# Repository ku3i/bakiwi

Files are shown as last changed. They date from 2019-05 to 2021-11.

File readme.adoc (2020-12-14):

= Bakiwi
Doc Writer <kubisch@informatik.hu-berlin.de>
v0.1, 2020-04-02
:imagesdir: ./images/

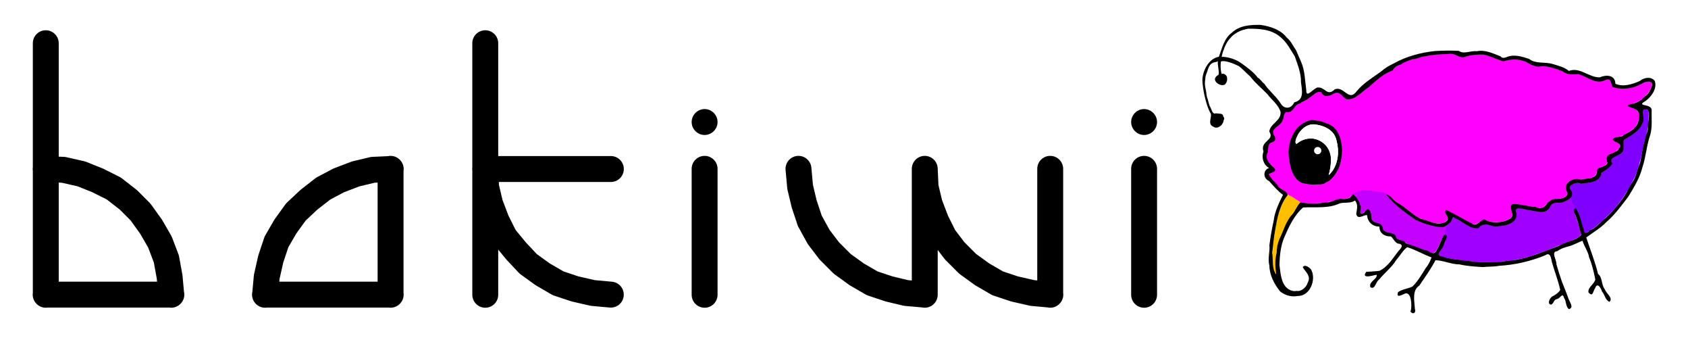
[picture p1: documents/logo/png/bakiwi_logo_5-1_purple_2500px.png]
Bakiwi


== The fabulous DIY walking robot kit.

_tl;dr: Build your own walking robot._

Welcome to the Bakiwiverse.

Bakiwis are small walking robots with only two motors that come as a kit and are easy to build. Each Bakiwi is unique. You can freely choose how it will look and behave. You can easily change your Bakiwi's walking style with four knobs mounted on the printed circuit board. Programming is not required, but have a look into the _source_ folder if you like to modify the firmware and add some nice features.

Bakiwis combine education and fun and are therefore perfect for teaching robotics to children and beginners. We have already built dozens of Bakiwis in many workshops and the builders are always amazed when their robot creature starts to walk. While it is fun to build and play with the bakiwis, many skills and technical experience are acquired.

For information on ongoing developments, you might want to follow the project on its link:https://hackaday.io/project/169268-bakiwi-robot[hackaday.io page] or follow me on link:https://twitter.com/qbernetik[twitter/@qbernetik]

== Assembly Manual

Here you can find the link:https://github.com/ku3i/Bakiwi/tree/master/manual[Bakiwi Assembly Manuals] in English and German language.

== Get a Bakiwi

We at Jetpack Cognition Lab develop, manufacture, and distribute Bakiwi Robots in our home base in Berlin/Germany. All electronic parts are RoHS compliant and the 3D-printed parts are made from PLA which is plant-based and is industrially compostable. The production of the kits takes place in Berlin-Friedrichshain and under fair conditions. If you want to *buy a Bakiwi Kit*, please visit our store: link:https://bakiwi.shop[] or consider supporting our link:https://www.kickstarter.com/projects/bakiwi/bakiwi-invent-a-robot-friend[kickstarter campaign]. 

== Videos

****
There are some video links available on how _Bakiwi_ could look when assembled and how it performs:

* link:https://www.youtube.com/watch?v=UyHHptdRnA0[Ministry of Silly Walks]
* link:https://www.youtube.com/watch?v=r7zon1IOzuM[Pulling Things]
* link:https://www.youtube.com/watch?v=ixKAcRevgqk[Bakiwicalypse]
* link:https://www.youtube.com/watch?v=EbDHLbfVccA[Human Sensing]
* link:https://www.youtube.com/watch?v=psynHG6JsZE[Workshop CCCamp19]
* link:https://www.youtube.com/watch?v=GNrDzkgFEy4[Where can I get a Bakiwi?]
****

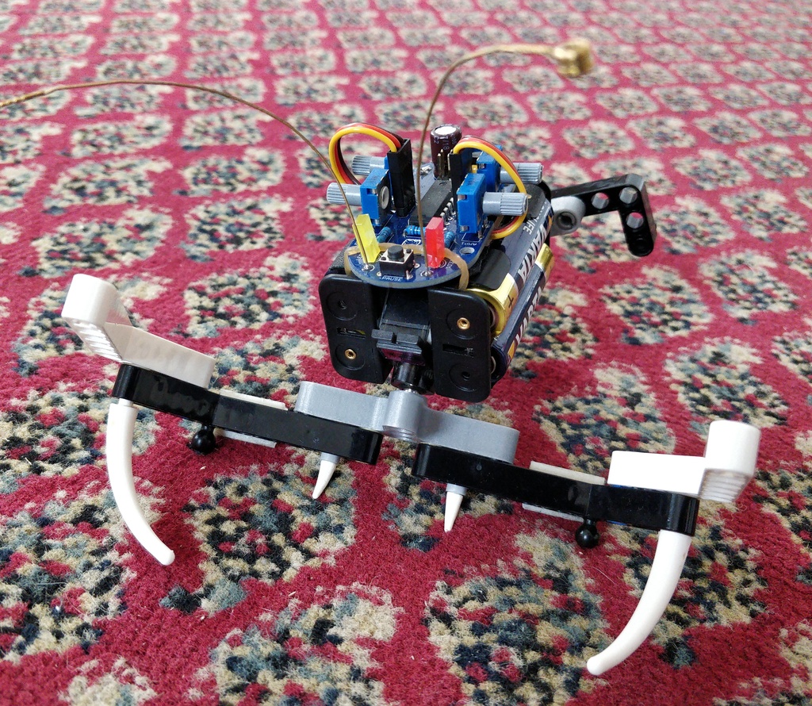
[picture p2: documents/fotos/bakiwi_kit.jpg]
Bakiwi


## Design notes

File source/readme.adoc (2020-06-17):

= Bakiwi Firmware Help
Doc Writer <kubisch@informatik.hu-berlin.de>
v0.1, 2020-04-02
:imagesdir: ./img
:toc:

_This is the Bakiwi Kit Firmware Section. Depending on your Bakiwi's hardware revision, you have to choose between different software versions._

All files of the Bakiwi firmware code is free/libre open-source software. The firmware is currently written in C/C++ incorporating the Arduino framework and some external libraries. The firmware can be deployed using the Arduino IDE.

* so2walk
* bakiwi_kit
* bakiwi_sen (*)
* plops (*)

_(*)this firmware is still under heavy development and may be subject to larger changes._

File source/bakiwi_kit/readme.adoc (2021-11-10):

= Bakiwi Install Firmware Manual
Doc Writer <kubisch@informatik.hu-berlin.de>
v0.3, 2021-11-10
:toc:

:imagesdir: ./doc

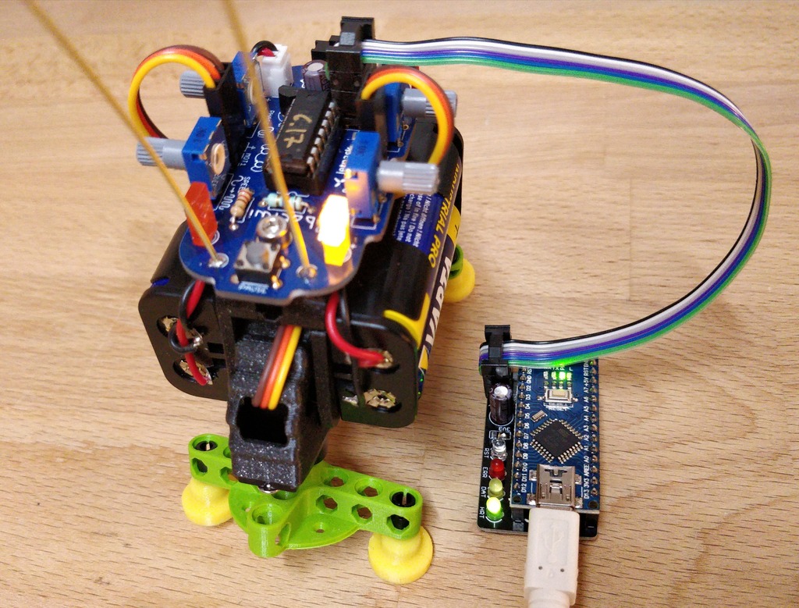
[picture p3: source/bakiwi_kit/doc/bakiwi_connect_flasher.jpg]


These instructions describe how to install or update firmware on your Bakiwi and also enable you to install a self-written program.

== Get the Programmer Device
In order to upload software to your Bakiwi you need a programmer device capable of handling AVR microcontrollers such as the Microchip ATtiny84.

There is plenty of AVR programmers available and most of them should do the job nicely. However if you are new to programming AVR microcontrollers we recommend using the ArduinoISP Kit as it works nicely together with the Arduino Integrated Development Environment (IDE).

Along with the Bakiwi Robot Kit there is the possibility to purchase a Bakiwi Programmer which comes as a solder kit.
****
`https://bakiwi.shop`
****

At the end of this document, there can be found advice on how to assemble the programmer kit.

== Get the Source Code
Clone the repository or get it via Github's download button:
****
`git clone https://github.com/ku3i/bakiwi`
****

This step requires `git`. If you're on a Linux machine, you probably have `git` already installed. You can test this by opening a terminal and typing `git --version`. If `git` is not yet installed and you want to install it, type:
****
`sudo apt-get install git`
****

== Installing the Firmware

=== Get latest Arduino IDE
Open a Browser, navigate to the following link and download the latest version of the Arduino IDE (we tested this documentation with version 1.8.12):
****
`https://www.arduino.cc/en/Main/Software`
****
=== Setup ATtiny84 Support for Arduino IDE
Start the IDE and open the `preferences` dialog. Add the following link to `Additional Boards Manager URLs`:
****
`https://raw.githubusercontent.com/damellis/attiny/ide-1.6.x-boards-manager/package_damellis_attiny_index.json`
****

Then select `Tools -> Board -> Boards Manager` and seach for `attiny`. Install the `Attiny Support Library by Davis A. Mellis`.

=== Open the Firmware Source Code and Setup Microcontroller
When the installation was succesfull open the `source/bakiwi_kit/so2walk_tiny/so2walk_tiny.ino` file via `File -> Open` dialog and setup the Attiny84 processor in `Tools` accordingly as described in the picture:

* Board: *ATtiny24/44/84*
* Processor: *ATtiny84*
* Clock: *Internal 8 MHz*
* Programmer: *Arduino as ISP* (if using a Bakiwi-ISP)

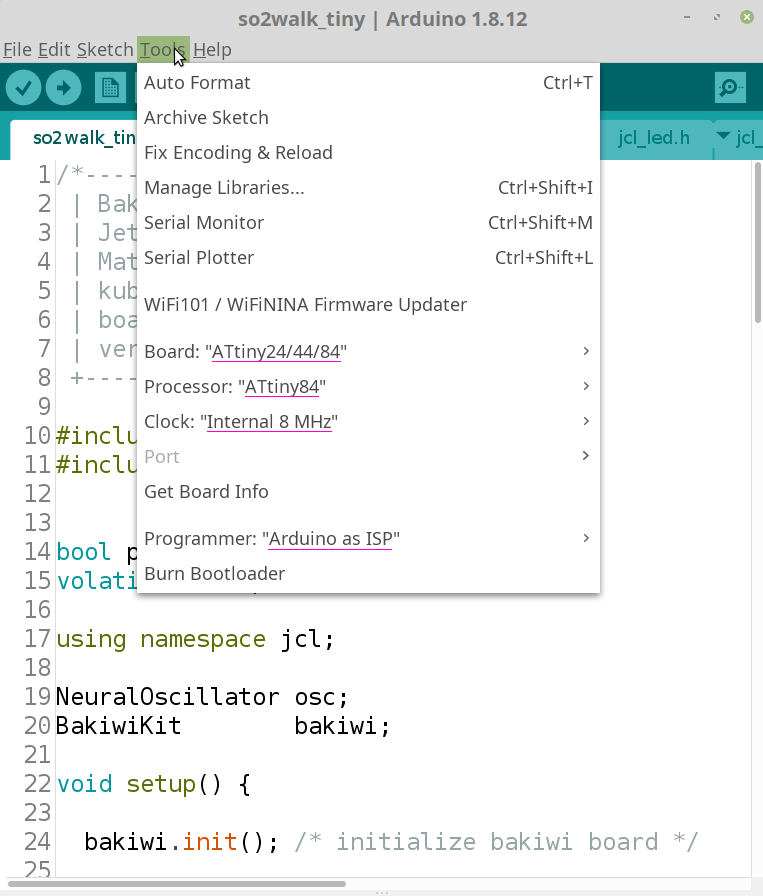
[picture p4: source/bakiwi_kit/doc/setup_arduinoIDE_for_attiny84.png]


=== Compile and Upload the Firmware

If you have set up the processor, select `Sketch -> Verify/Compile` and if the code could be successfully compiled, connect the Bakiwi-Programmer to your computer via USB cable and to your Bakiwi via the 6-pin ISP connector (pay attention to the polarity).

Then select `Sketch -> Upload` and the programmer should now start to flash the LEDs for some seconds. After that, remove the 6-pin ISP connector.

The Bakiwi-Firmware should now be installed.

== Bakiwi Programming for Experts
Your Bakiwi is always delivered with the latest firmware. However, if you want to use a brand new ATTiny84, the fuses must first be set. The following commands do exactly this and cause the LEDs to flash as a success message. You can also use the minimal program as a starting point for your own firmware development if you do not want to use the Arduino IDE or the Arduino framework.

=== Get AVR Toolchain
Make sure you have a minimal AVR toolchain installed (Linux).
****
`sudo apt-get install gcc-avr binutils-avr avr-libc avrdude`
****

=== Set Fuses and Flash Helloworld
Navigate to the folder `source/blinky`:
****
`cd source/bakiwi_kit/blinky`
****

Then build, test and install the Bakiwi's Helloworld (blinky) program by typing:
****
`make`

`make test`

`make install`
****

This sets the fuses of the ATtiny84 and causes the LEDs to flash at a rate of around 1 Hz. If the fuses are once set, and you're not going to change them, you can also only flash the program without further touching the fuses:
****
`make flash`
****

=== Programmer Assembly
Like the Bakiwi, the programmer comes as a kit and needs to be soldered together as shown in the pictures below. We recommend starting by soldering the two 15-pin headers onto the blue Arduino-compatible board.

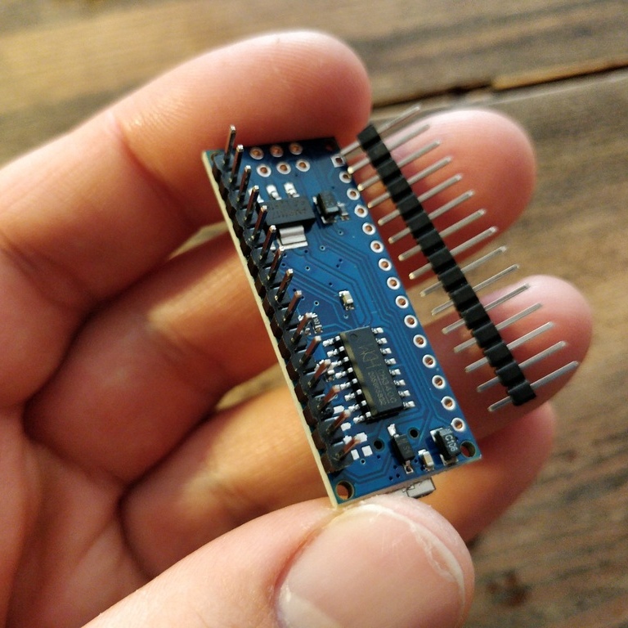
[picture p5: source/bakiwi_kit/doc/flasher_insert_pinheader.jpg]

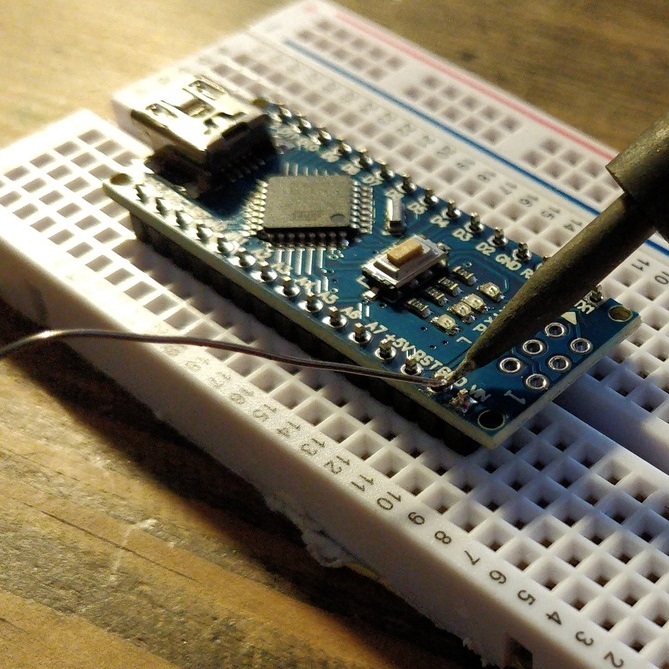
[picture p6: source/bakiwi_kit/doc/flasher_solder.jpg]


Next, you need to solder the components to the daughterboard as shown below. If you have no soldering expertise so far, we recommend starting with the Bakiwi-Kit before soldering the programmer.

The component in your kit are:

* 7x resistor 1 kOhms
* 4x LEDs of different colors
* 1x electrolytic capacitor
* Arduino-Nano compatible board
* 2x pin headers (15 pins)
* 2x sockets (15 pins)
* 1x 6-wire flat cable
* 2x cable end sockets with clamps
* 1x pin header (2x3 pins)

All parts are inserted from the top side of the circuit board (marked with the Jetpack logo) and soldered from the bottom side.

[NOTE]
====
The electrolytic capacitor has polarity, so you need to solder the long wire to the solder pad marked with the plus sign.
====

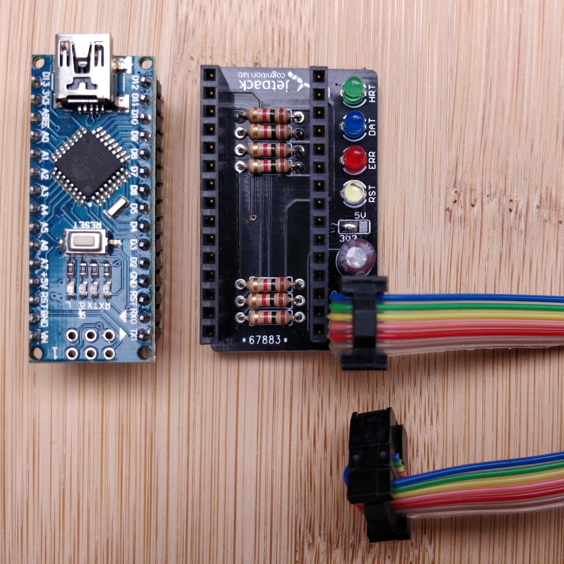
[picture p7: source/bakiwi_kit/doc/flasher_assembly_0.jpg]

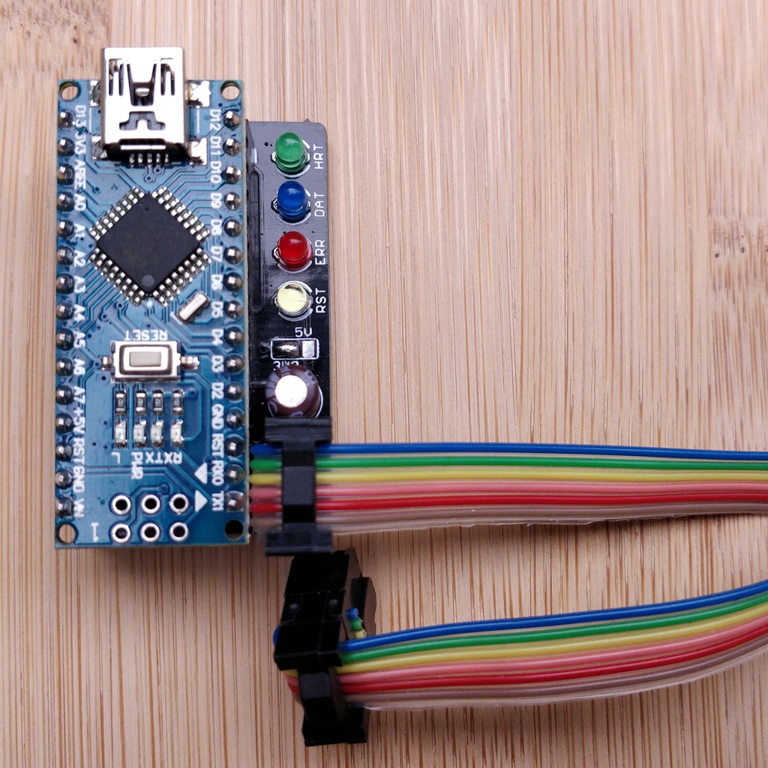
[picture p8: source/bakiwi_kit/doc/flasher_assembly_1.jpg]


For programming Bakiwis the device must be configured for providing a voltage of 3.3V. Make sure to bridge the solder pads close to the 3V3 sign.

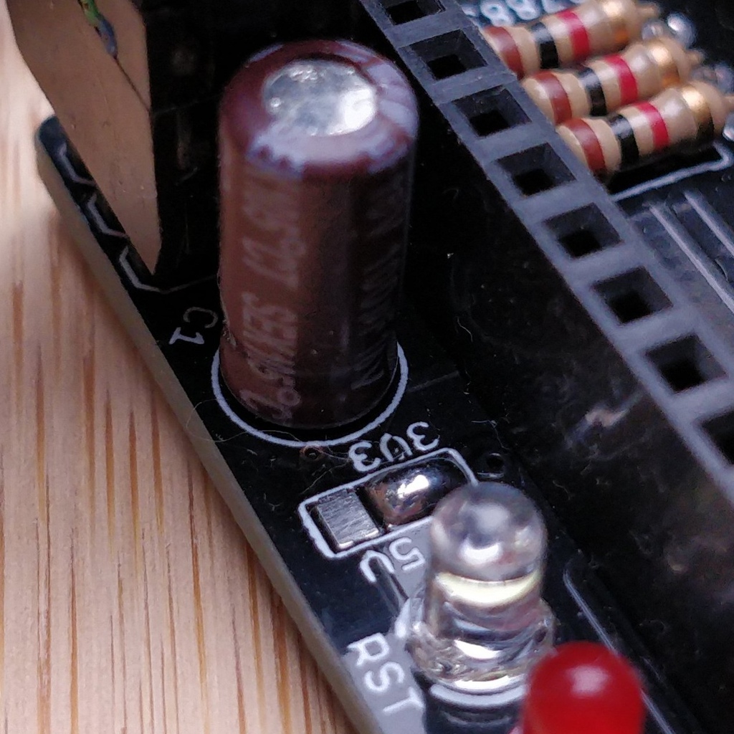
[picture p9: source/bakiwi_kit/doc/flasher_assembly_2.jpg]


Before you can use it, the programmer needs its own software.
Start the Arduino IDE and open the code example **File->Examples->11.ArduinoISP** .
The code should be uploaded using the settings shown below:

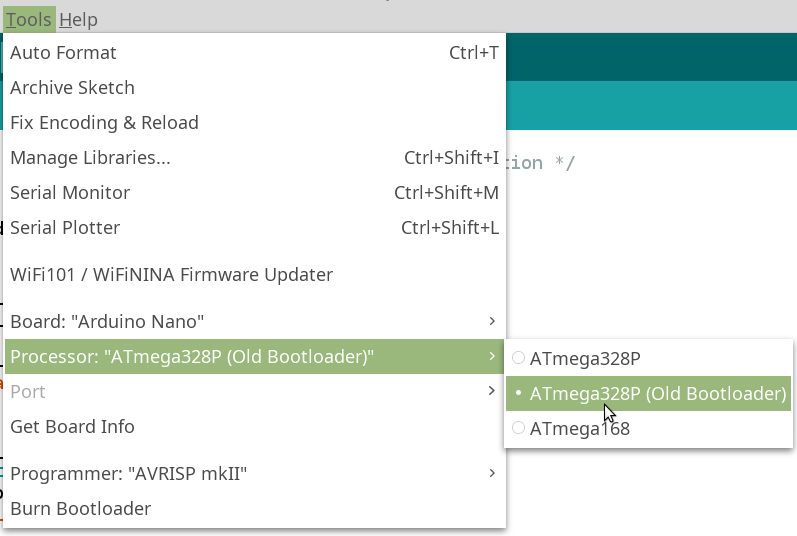
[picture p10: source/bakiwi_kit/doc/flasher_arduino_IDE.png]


[NOTE]
====
In order to upload the programmers code the blue-colored Arduino-Nano compatible board must *not* be connected to the daughter board, since the electrolytic capacitor is (intentionally) preventing the device from receiving the reset command from the computer.
====

After successfully uploading the ArduinoISP code the boards can be put together and are ready to be used as a programmer device.

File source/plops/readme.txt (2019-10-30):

+ goto 'blinky' first
    + type make
    + type make install
    + sets fuses to use internal clock w/o prescaler,
    + should blink the led at 1Hz

+ in arduino IDE
    + install Attiny support library: "attiny by Davis A. Mellis"
    + https://create.arduino.cc/projecthub/arjun/programming-attiny85-with-arduino-uno-afb829
    + see setup_IDE.png

+ compile and upload

+ when led is defined as 'front',
    + left poti sets amplitude and difference,
    + right poti sets frequency and phase

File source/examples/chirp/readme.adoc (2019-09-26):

= Bakiwi Chirp Test
Doc Writer <kubisch@informatik.hu-berlin.de>
v0.1, 2019-09-25

_This is the Chirp manual. With the following you can assemble your own bird-like chirping device with only a few components._

=== Components

* breadboard + wire bundle
* Arduino Nano (or compatible board)
* 10k potentiometer
* piezo buzzer

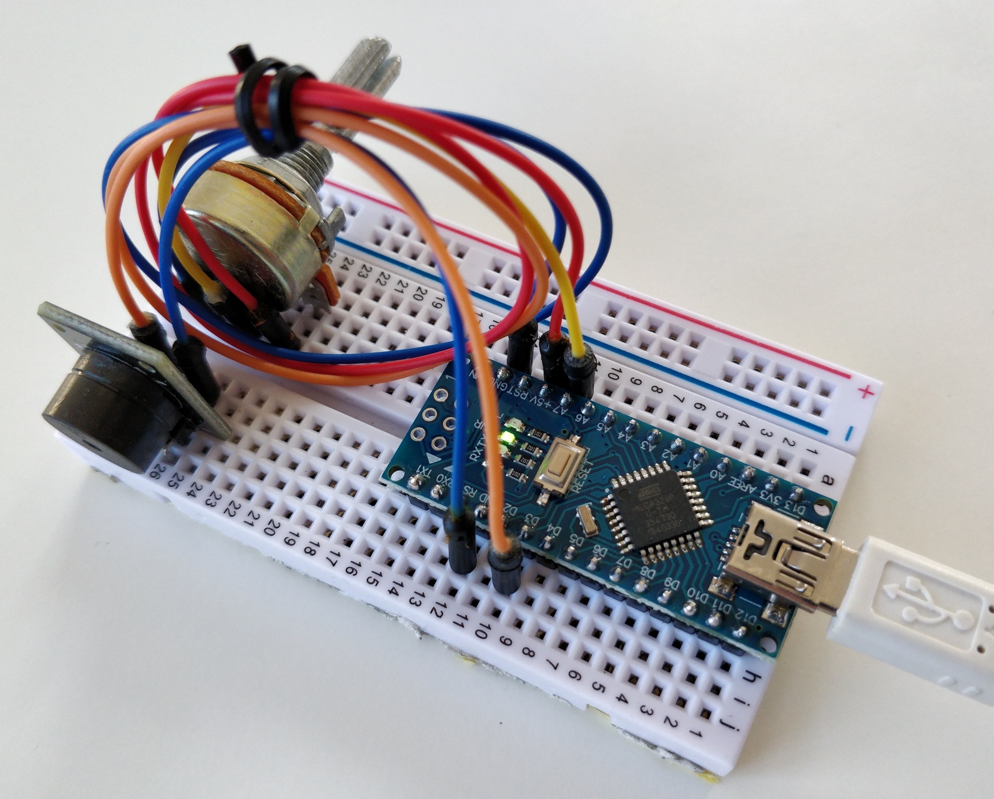
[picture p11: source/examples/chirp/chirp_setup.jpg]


=== Assembly

Connect the potentiometer as a voltage divider (V+,signal,GND) with 'signal' to one of the microcontroller's ADC input pins (e.g. A7).
Connect the piezo to GND and one of the microcontroller's digital output pins (e.g. D3).
Flash the program.

=== Explanation

The basic mechanism for the simple bird-like sound is to exponentially sweep down the frequency from something aroung 6 KHz to something around 4 KHz.
The sweep is further modulated by a slower oscillation and all parameters (including waiting times) are randomized to appear more natural and less technical/predictable.

The potentiometer is for regulating the chirps base-frequency.

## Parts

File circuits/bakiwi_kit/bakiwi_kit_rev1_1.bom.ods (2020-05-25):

Size of Charge | 100
Part name | count | Price p.p. | Sum | total count | Charge | Distributor | Art.-No. | Specific parts name | Link
Motherboard | 1 | 3,00 € | 3,00 € | 100 | 300,00 € | Jetpack | JCL-Bakiwi-Kit-PCB-rev.1.1 | Bakiwi printed circuit board | via tindie
Micro-Servo | 2 | 5,80 € | 11,60 € | 200 | 1.160,00 € | Hobbyking | 026000012-0 | Towerpro MG90D Mini Digital Servo | https://hobbyking.com/de_de/towerpro-mg90d-mini-digital-servo-2-4kg-0-08sec-13g.html
Tactile Switch | 1 | 0,15 € | 0,15 € | 100 | 15,00 € | Reichelt | RND 210-00193 | Printtaster, THT, 2,45 N, 6 x 6 x 5 mm | https://www.reichelt.de/printtaster-tht-2-45-n-6-x-6-x-5-mm-rnd-210-00193-p226414.html
Slide Switch | 1 | 0,56 € | 0,56 € | 100 | 56,00 € | Reichelt | SS ESP101 | Schiebeschalter 1x UM, stehend, Print, RM 2,54 | https://www.reichelt.de/schiebeschalter-1x-um-stehend-print-rm-2-54-ss-esp101-p112178.html
Potentiometer | 4 | 0,25 € | 1,00 € | 400 | 100,00 € | Reichelt | ACP 9-SRS 10K | Einstellpotentiometer, stehend, 10 kOhm, 9 mm | https://www.reichelt.de/einstellpotentiometer-stehend-10-kohm-9-mm-acp-9-srs-10k-p111802.html
Knob for Pot. | 4 | 0,07 € | 0,28 € | 400 | 28,00 € | Reichelt | ACHSE ACP 9 G | Steckachse, Ø5 x 10 mm, grau | https://www.reichelt.de/steckachse-5-x-10-mm-grau-achse-acp-9-g-p111812.html
Battery Holder | 2 | 0,27 € | 0,54 € | 200 | 54,00 € | BerryBase | 46552 | Batteriehalter für 2x Mignon AA mit Lötanschluss | https://www.berrybase.de/strom/batterien-akkus/installation-zubehoer/batterie-clips-halter/batteriehalter-fuer-mignon/batteriehalter-f-252-r-2x-mignon-aa-mit-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
Capacitor 100nF | 1 | 0,07 € | 0,07 € | 100 | 7,00 € | Digikey | 399-4151-ND‎ | KEMET C315C104M5U5TA, CAP CER 0.1UF 50V Z5U RADIAL | https://www.digikey.de/product-detail/de/C315C104M5U5TA/399-4151-ND/817927/
Capacitor 100µF | 1 | 0,02 € | 0,02 € | 100 | 2,00 € | Reichelt | RAD 100/16 | Elko, radial, 100 µF, 16 V, RM 2,5, 85°C, 2000h, 20% | https://www.reichelt.de/elko-radial-100-f-16-v-rm-2-5-85-c-2000h-20-rad-100-16-p15101.html
Pinheader | 2 | 0,07 € | 0,14 € | 200 | 14,00 € | Reichelt | MPE 087-1-003 | Stiftleisten 2,54 mm, 1X03, gerade | https://www.reichelt.de/stiftleisten-2-54-mm-1x03-gerade-mpe-087-1-003-p119880.html
Resistor 220 Ohm | 2 | 0,08 € | 0,16 € | 200 | 16,00 € | Reichelt | K-O RD14JN221T52 | Widerstand, Kohleschicht, 220 Ohm, 0207, 250 mW, 5% | https://www.reichelt.de/widerstand-kohleschicht-220-ohm-0207-250-mw-5-k-o-rd14jn221t52-p237384.html
LED yellow | 1 | 0,10 € | 0,10 € | 100 | 10,00 € | Reichelt | EVL 1533UYD/S530 | LED, rechteckig, 2,4x5 mm, bedrahtet, gelb, 20 mcd, 180° | https://www.reichelt.de/led-rechteckig-2-4x5-mm-bedrahtet-gelb-20-mcd-180-evl-1533uyd-s530-p231052.html
LED red | 1 | 0,09 € | 0,09 € | 100 | 9,00 € | Reichelt | EVL 1533SURD/S53 | LED, rechteckig, 2,4x5 mm, bedrahtet, rot, 20 mcd, 170° | https://www.reichelt.de/led-rechteckig-2-4x5-mm-bedrahtet-rot-20-mcd-170-evl-1533surd-s53-p231051.html
attiny84 | 1 | 0,85 € | 0,85 € | 100 | 85,38 € | Digikey | ATTINY84A-PU-ND‎ | ATTINY84A-PU‎, IC MCU 8BIT 8KB FLASH 14DIP | https://www.digikey.de/product-detail/de/ATTINY84A-PU/ATTINY84A-PU-ND/2774082/
IC Socket, 14pin | 1 | 0,05 € | 0,05 € | 100 | 5,00 € | Reichelt | GS 14 | IC-Sockel, 14-polig, doppelter Federkontakt | https://www.reichelt.de/ic-sockel-14-polig-doppelter-federkontakt-gs-14-p8206.html
Voltage Regulator | 1 | 0,34 € | 0,34 € | 100 | 33,66 € | Digikey | LP2950ACZ-3.3GOS-ND | LP2950ACZ-3.3, IC REG LINEAR 3.3V 100MA TO92-3 | https://www.digikey.de/product-detail/de/on-semiconductor/LP2950ACZ-3.3G/LP2950ACZ-3.3GOS-ND/1476894
JST-Socket/Battery-Cable | 1 | 1,00 € | 1,00 € | 100 | 100,00 € | Amazon | TODO: find cheaper | 20 Stück Micro JST PH 2.0 2-Pin Stecker und 20 Stück 10 cm Rot und Schwarz Silikon Kabel Draht mit Buchse | https://www.amazon.de/St%C3%BCck-Stecker-Schwarz-Silikon-Buchse/dp/B07449V33P/
Price Material (Total) |  |  | 19,95 € |  | 1.995,04 €

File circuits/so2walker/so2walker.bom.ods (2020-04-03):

SO(2) Walker – Bill of Material
Part‘s Name | Count | Distributor | Art.-No. | Specific parts name (german)
Motherboard | 1 | Jetpack | JCL-PCB_SO2WALKER | SO(2) Walker Grundplatine
Arduino Nano 3.0 (comp.) | 1 | Makershop | 3323 | Nano V3.0 ATmega 328 Board
Micro-Servo | 2 | Hobbyking | 026000012-0 | Towerpro MG90D Mini Digital Servo
Tactile Switch | 1 | Reichelt | RND 210-00193 | Printtaster, THT, 2,45 N, 6 x 6 x 5 mm
Slide Switch | 1 | Reichelt | SS ESP101 | Schiebeschalter 1x UM, stehend, Print, RM 2,54
Potentiometer | 4 | Reichelt | ACP 9-SRS 10K | Einstellpotentiometer, stehend, 10 kOhm, 9 mm
Knob for Pot. | 4 | Reichelt | ACHSE ACP 9 G | Steckachse, Ø5 x 10 mm, grau
Battery Holder | 2 | Reichelt | HALTER 2XAAZ | Batteriehalter für 2 Mignonzellen (AA)
Capacitor 100nF | 1 | Reichelt | Z5U-2,5 100N | Vielschicht-Keramikkondensator 100N, 20%
Capacitor 100µF | 1 | Reichelt | M-A 100U 35 | Elko, radial, 100 µF, 35 V, RM 2,5, 85°C, 2000h, 20%
Pinheader | 4 | Reichelt | MPE 087-1-003 | Stiftleisten 2,54 mm, 1X03, gerade
Resitor 1K | 2 | Reichelt | AG 04FTE52-1K | Widerstand, Metallschicht, 1,0 kOhm, 0204, 0,4 W, 1%
LED grün | 1 | Reichelt | EVL 484-10SYGT | LED, 3 mm, bedrahtet, grün, 80°
LED rot | 1 | Reichelt | EVL 264-7SURD | LED, 3 mm, bedrahtet, rot, 125 mcd, 60°
Socket | 2 | Reichelt | MPE 094-1-016 | Buchsenleisten 2,54 mm, 1X16, gerade

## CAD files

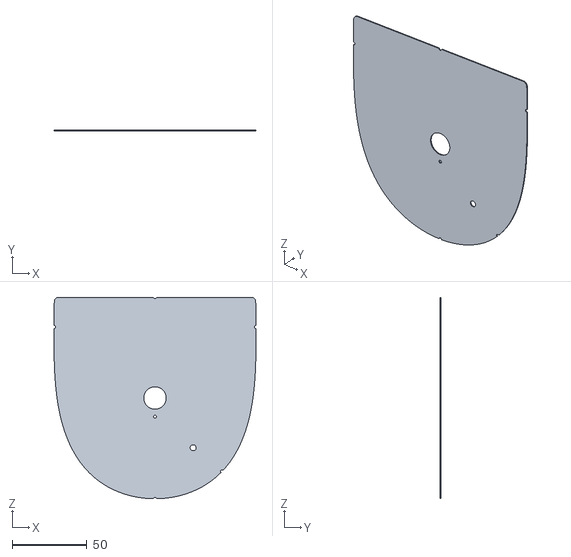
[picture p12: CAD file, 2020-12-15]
manual/apparel/stencil/cut_stencil.stl
135.3 x 0.6 x 135.0

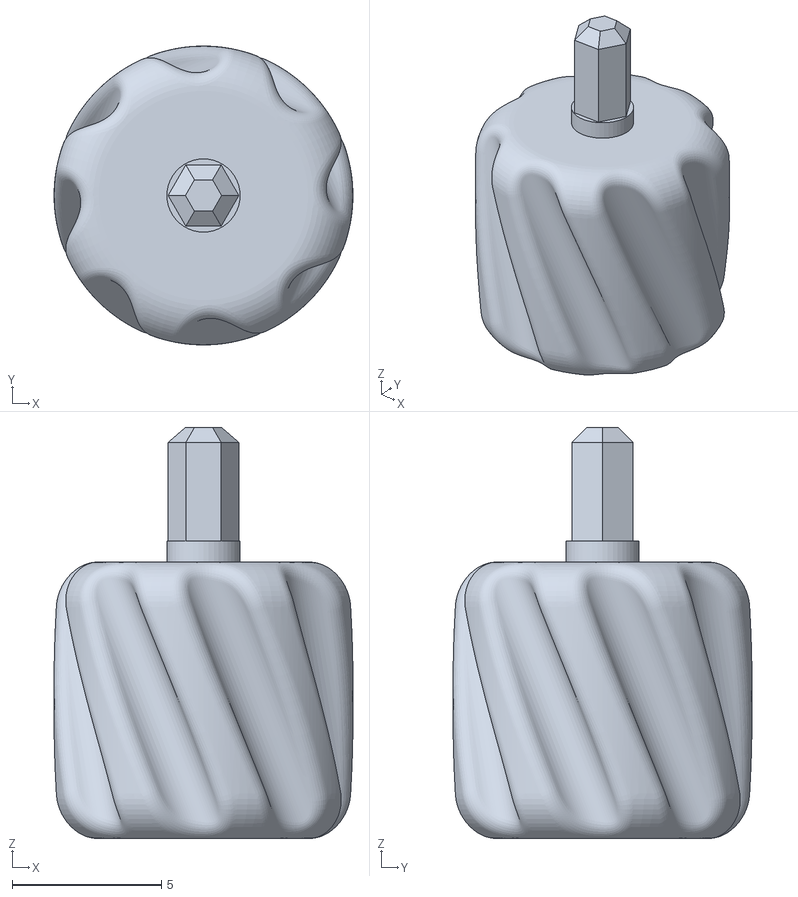
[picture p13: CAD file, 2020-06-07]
parts/frames/flex_ag/poti_knob.stl
10.00 x 10.00 x 13.8

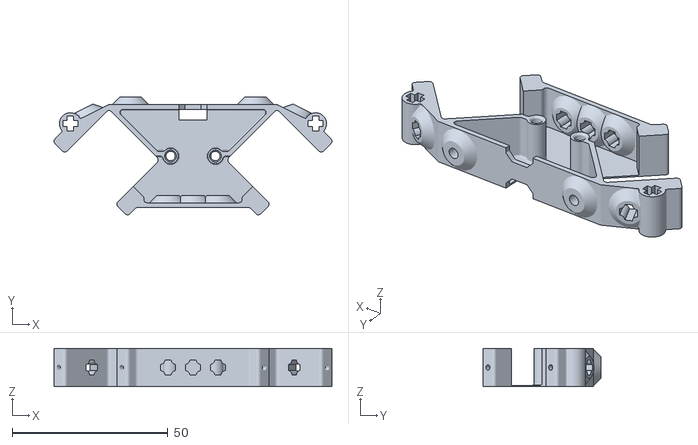
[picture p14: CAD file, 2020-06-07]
parts/frames/simple/simple_symmetric_frame_rev1.stl
89.2 x 37.8 x 12.2

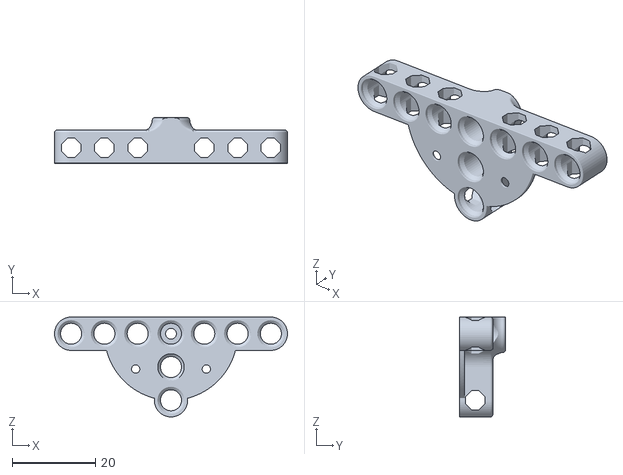
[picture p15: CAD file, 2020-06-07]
parts/horns/t-sect-3x7_multiuse_21T_UM3e_fine_0.stl
56.0 x 11.0 x 24.0

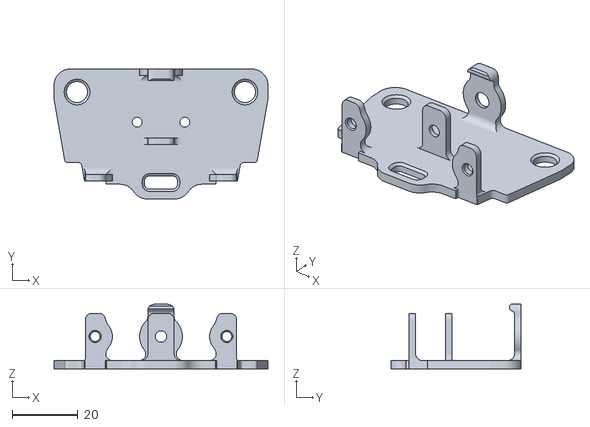
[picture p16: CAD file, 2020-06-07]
parts/frames/flex_ag/frame_base.stl
65.0 x 39.5 x 19.6

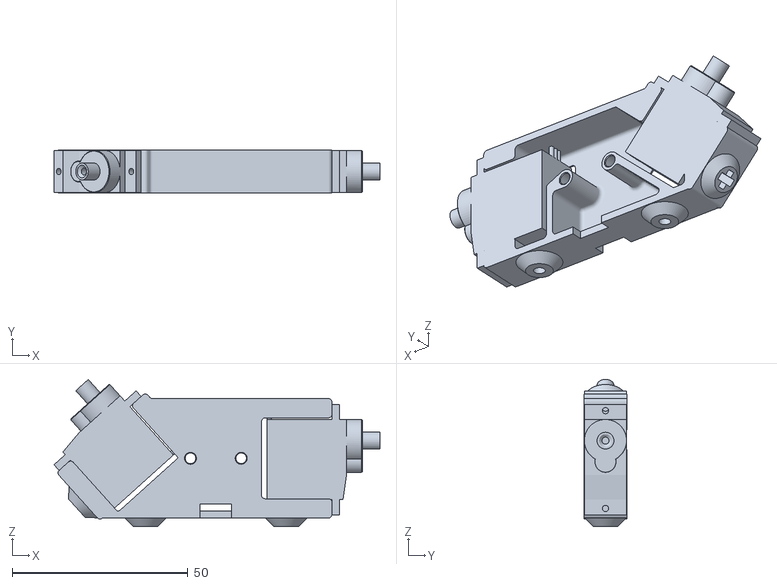
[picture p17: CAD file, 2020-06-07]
parts/frames/simple/simple_frame_rev1.stl
92.6 x 12.2 x 41.8

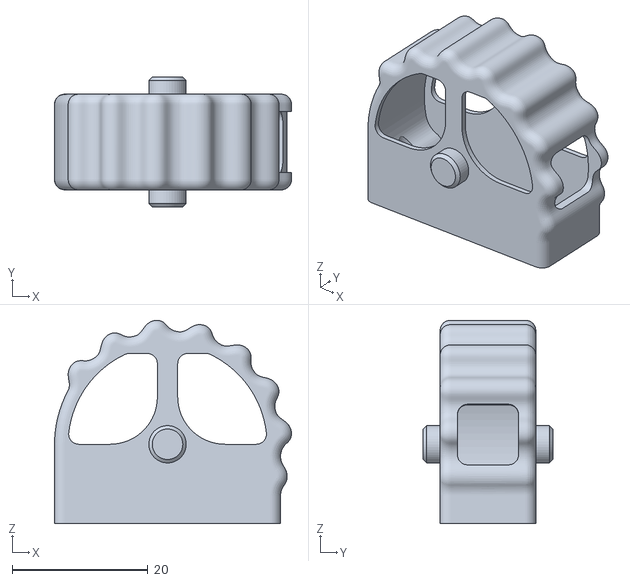
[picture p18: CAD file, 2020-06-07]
parts/frames/flex_ag/motor_holder_hedgehog.stl
34.9 x 19.1 x 30.0

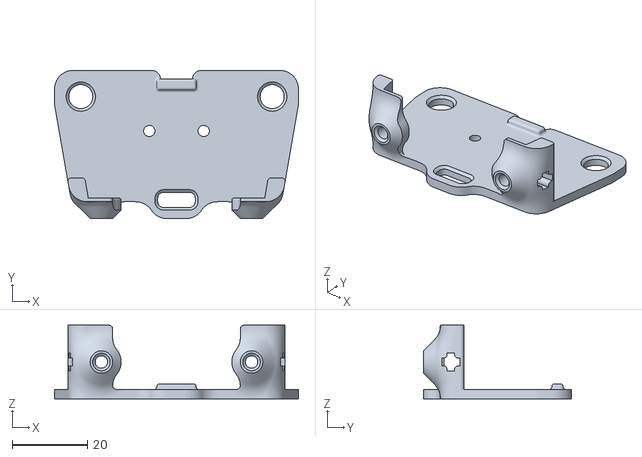
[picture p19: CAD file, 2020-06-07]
parts/frames/flex_ag/frame_lid.stl
65.0 x 39.5 x 19.6

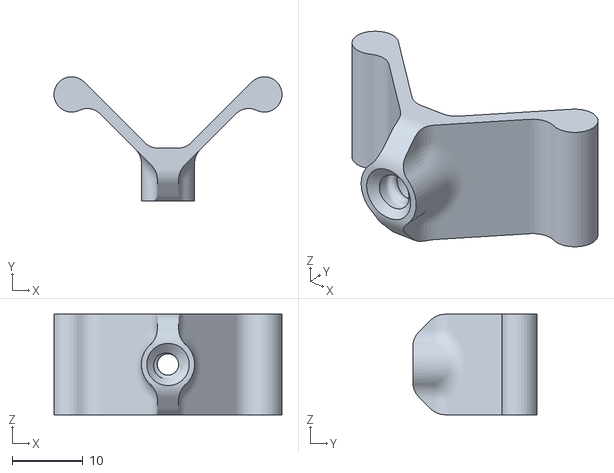
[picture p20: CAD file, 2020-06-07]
parts/frames/flex_ag/clamp_nut.stl
32.2 x 17.6 x 14.2

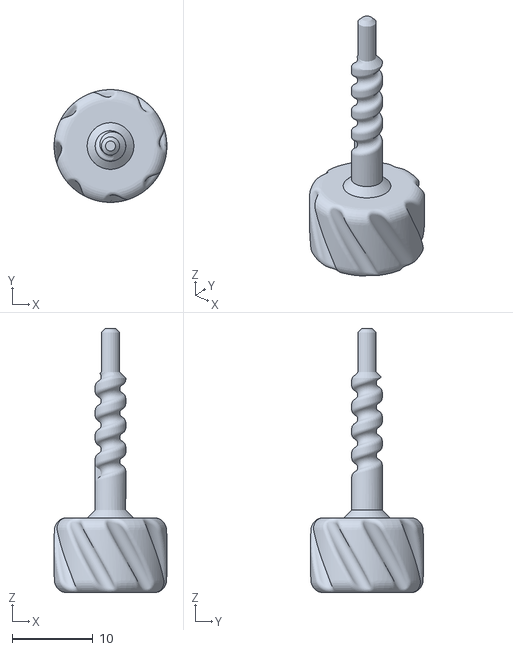
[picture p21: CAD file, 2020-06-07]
parts/frames/flex_ag/locking_screw.stl
14.0 x 14.0 x 32.8

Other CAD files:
parts/horns/t-sect-3x7_multiuse_20T_UM3e_fine_0.stl

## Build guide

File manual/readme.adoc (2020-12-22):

= Bakiwi Assembly Manuals / Bauanleitungen
Doc Writer <kubisch@informatik.hu-berlin.de>
v0.2, 2020-12-15
:imagesdir: ./bakiwi_kit/img
:favicon: {imagesdir}/icons/favicon.png
:stylesheet: ./bakiwi_kit/bak.css
:toc:
:toc-placement!:
:toc-title: Contents/Inhalt

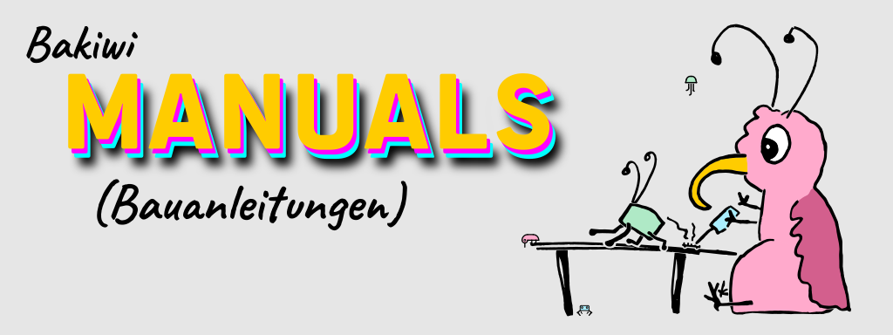
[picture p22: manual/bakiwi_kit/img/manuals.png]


toc::[]

== Welcome / Willkommen

*EN* Here you can find the Bakiwi Kit solder and assembly manuals. Depending on your Bakiwi's hardware revision, you have to choose between different versions of the manual. All files of the Bakiwi assembly manuals are under the CREATIVE COMMONS LICENSE CC-BY-NC-SA. Our manuals are written in the fabulous link:https://asciidoctor.org/docs/what-is-asciidoc/[AsciiDoc] markup language.

*DE* Hier finden Sie die Bakiwi Kit Löt- und Montageanleitungen. Abhängig von der Hardwareversion Ihres Bakiwi, müssen Sie zwischen verschiedenen Versionen des Handbuchs wählen. Alle Dateien der Bakiwi-Montageanleitungen stehen unter der CREATIVE COMMONS-LIZENZ CC-BY-NC-SA. Unsere Handbücher sind in der fabelhaften link:https://asciidoctor.org/docs/what-is-asciidoc/[AsciiDoc] Markup-Sprache geschrieben.

== Bakiwi Kit

=== Assembly / Zusammenbau
link:https://github.com/ku3i/Bakiwi/blob/master/manual/bakiwi_kit/EN_manual_bakiwi_kit_rev_1_1.adoc[EN - Assembly Instructions in English]

link:https://github.com/ku3i/Bakiwi/blob/master/manual/bakiwi_kit/DE_manual_bakiwi_kit_rev_1_1.adoc[DE - Bauanleitung auf Deutsch]

=== Sewing / Nähen
link:https://github.com/ku3i/Bakiwi/blob/master/manual/apparel/EN_bakiwi_kit_apparel.adoc[EN - Sewing Instructions in English]

link:https://github.com/ku3i/Bakiwi/blob/master/manual/apparel/DE_bakiwi_kit_apparel.adoc[DE - Nähanleitung auf Deutsch]

== SO(2)-Walker

link:https://github.com/ku3i/Bakiwi/blob/master/manual/so2walker/readme.adoc[EN - Assembly Manual]

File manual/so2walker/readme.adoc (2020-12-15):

= Bakiwi Assembly Documentation
Doc Writer <kubisch@informatik.hu-berlin.de>
v0.2, 2020-04-02
:imagesdir: ./img
:toc:
:toc-placement!:
:stylesheet: ../bakiwi_kit/bak.css

_This is the old Bakiwi's assembly manual. If you bought your Bakiwi after June 2020 you are probably looking for link:../bakiwi_kit/EN_manual_bakiwi_kit_rev_1_1.adoc[the new manual]. With the following steps you can assemble your Bakiwi walking robot from the kit. We encourage everyone to contribute to this project. Please share your ideas and experiences, upgrades and schematics, source code and tricks._

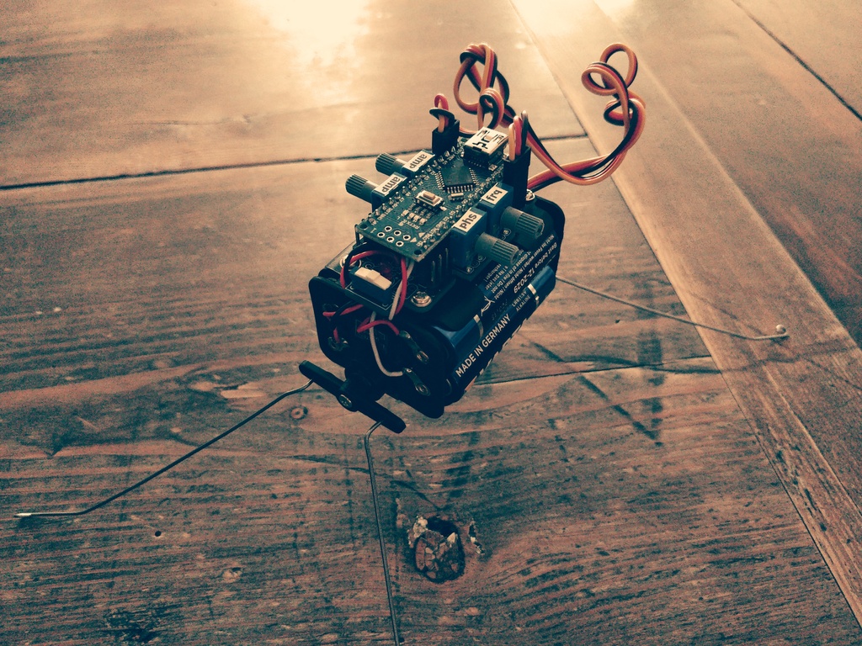
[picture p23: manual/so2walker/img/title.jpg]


== Motivation
****
There is some video links available on how _Bakiwi_ could look like when assembled and how it performs.

video: https://www.youtube.com/watch?v=UyHHptdRnA0[bakiwi robot with lego legs]

video::UyHHptdRnA0[youtube]

video: https://www.youtube.com/watch?v=lXEHFaAaYYs[bakiwi robot with spring steel legs live at xHain hack+makespace]

video::lXEHFaAaYYs[youtube]

****

toc::[]

== Preparation

NOTE: Before starting the assembly. Check that you have all the tools and parts in place. We recommend reading this manual once briefly before starting the assembly. Please also have a look at the link:/circuit/so2walker.sch.pdf[schematics] of the board or the board's link:/circuit/so2walker.brd.png[layout].

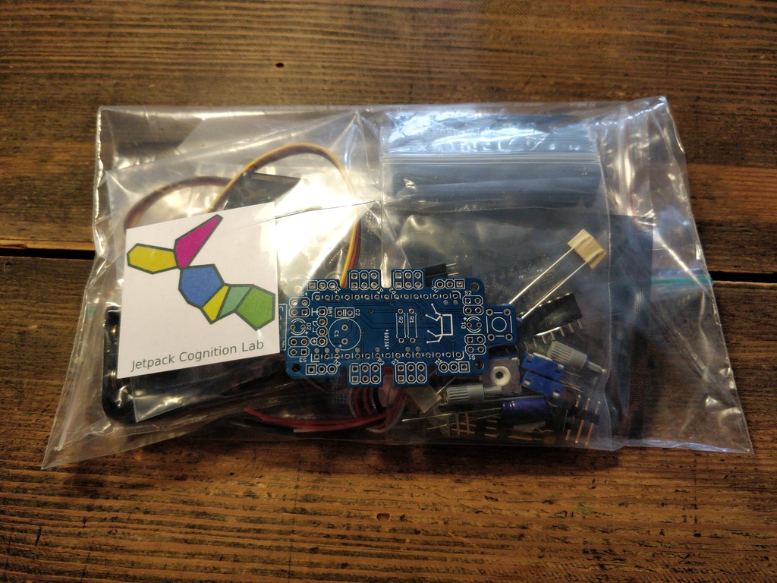
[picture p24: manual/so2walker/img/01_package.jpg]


=== Prepare Workbench and Tools

****
Clean and wipe your workbench and get all the tools needed as denoted in the list or shown in the picture.
****

=== Recommended Tools

We recommend these tools to assemble the _Bakiwi_ robot:

* soldering iron with a very fine tip and solder (0.5mm) and up to 400°C (regulated) temperature
* flat-nosed pliers
* side-cutting pliers
* wire stripper
* utility knife
* multimeter
* sandpaper or files
* small Phillips screw driver
* tweezers (optionally)
* hot glue or superglue (optionally)
* a box of craft materials, trash or old Lego parts for creating legs and body parts of your robot.

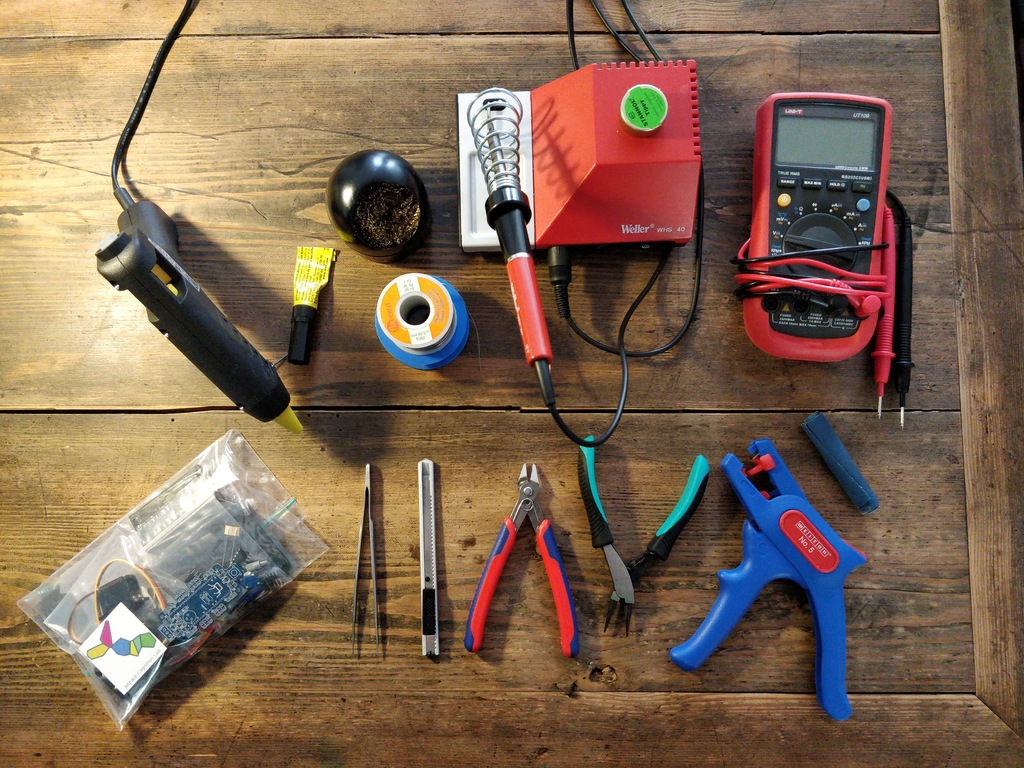
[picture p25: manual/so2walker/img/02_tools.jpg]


=== Check the Parts

TIP: Check the parts in your _Bakiwi_ package for completeness and complain to link:mailto:kubisch@informatik.hu-berlin.de[me via email] if it's not complete :)

=== Bakiwi Assembly Kit Parts

[cols=2*]
|===
| 2 | micro servos (incl. several horns)
| 4 | mini-potentiometers 10 kΩ
| 4 | mini-knob
| 1 | PCB _SO(2)-Walker_ (referred to as the _motherboard_)
| 1 | Arduino-Nano compatible board (i.e. _Nano-Board_)
| 2 | battery holder (2xAA)
| 2 | 1 kΩ resistor
| 2 | LED (two different colors)
| 4 | 1x3 pin header
| 2 | 1x15 socket
| 1 | 100 µF electrolytic capacitor
| 1 | 100 nF ceramic capacitor
| 1 | tactile button
| 2 | on/off slide switch
| 4 | 10 cm cable
|===

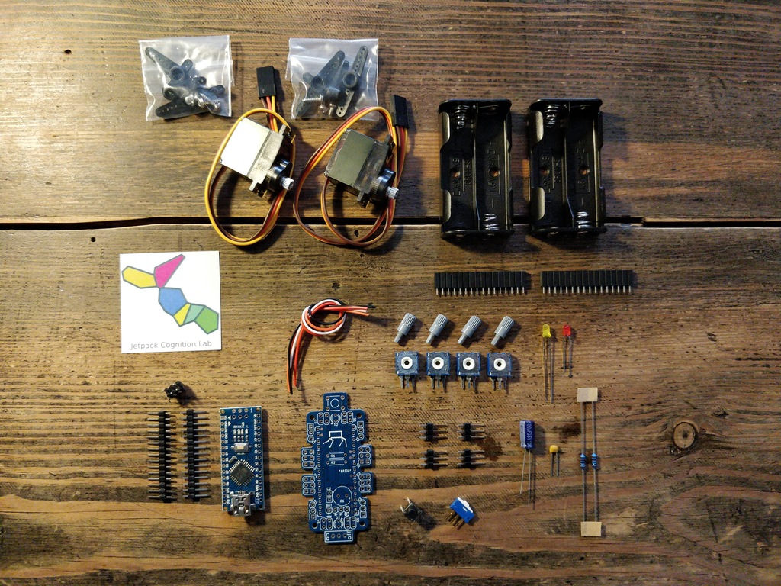
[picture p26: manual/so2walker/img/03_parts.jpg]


IMPORTANT: Batteries might not be included in the set. Ask your workshop leader or get you a set of 4x AA (mignon) batteries with 1.5 Volts each.

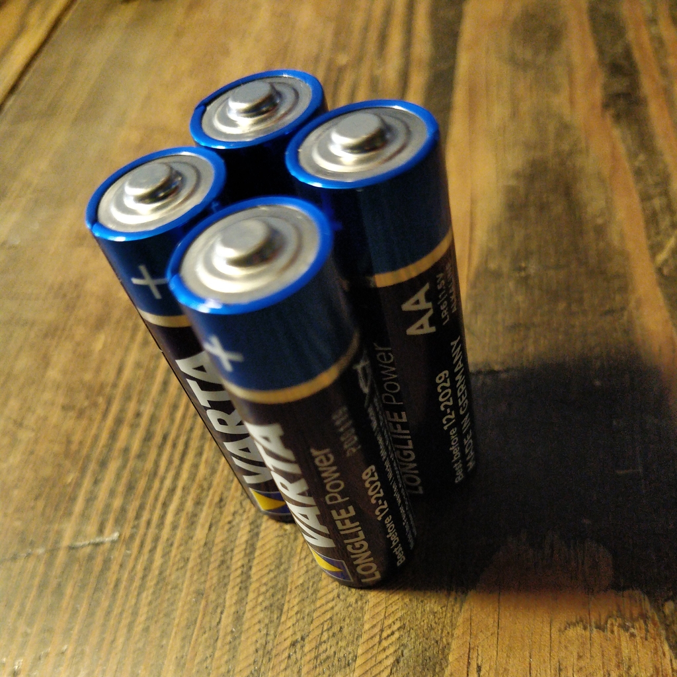
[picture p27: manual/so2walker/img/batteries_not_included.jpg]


== Soldering

=== Prepare Soldering
****
Prepare your workbench for soldering. We recommend using a fine tip and thin solder.
****

IMPORTANT: Watch your health! Use enough light. Make sure there is fresh air during soldering and not to breath-in the solder vapor.

CAUTION: Soldering irons get REALLY hot. You need to stay focused and should be careful not to burn yourself or others. When leaving the table or room, switch off the soldering station.

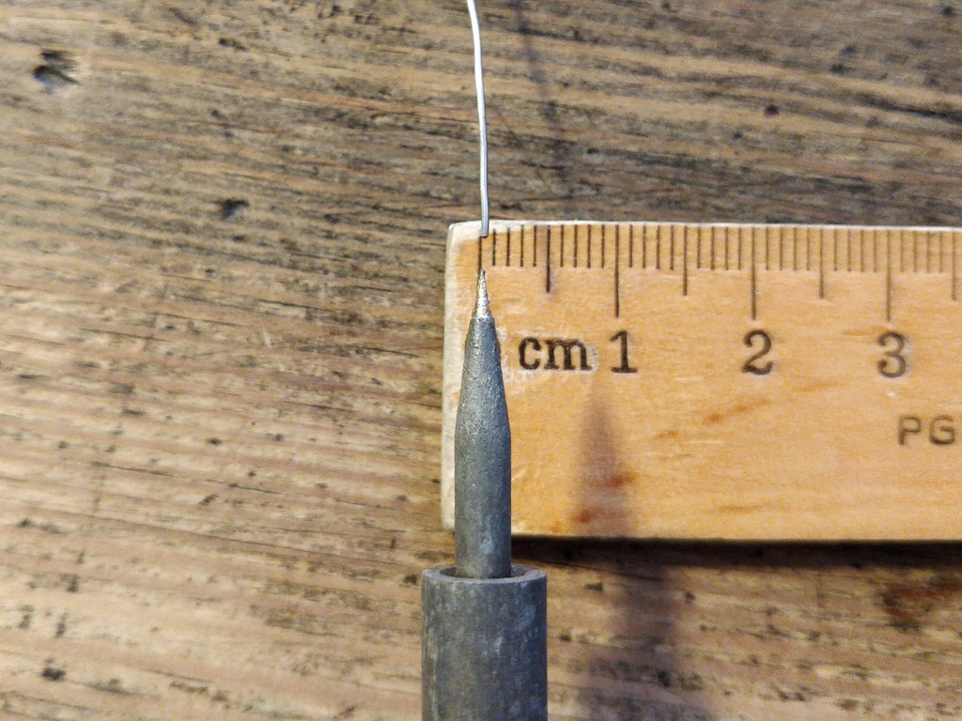
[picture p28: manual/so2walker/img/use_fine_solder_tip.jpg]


****
Adjust the soldering station for sufficient heat depending on the solder you use. Some stations show the current temperature, make sure to let the iron pre-heat before starting. If soldering 'feels' very sticky, you might have not the correct temperature (too cold) or the flux in the molten solder has already evaporated. Also, ensure to always use a clean solder tip, preferably using a dry cleaner (metal pot cleaner) as it does not cool down the solder tip (in comparison to a wet sponge) and the cleaning result is generally better.
****

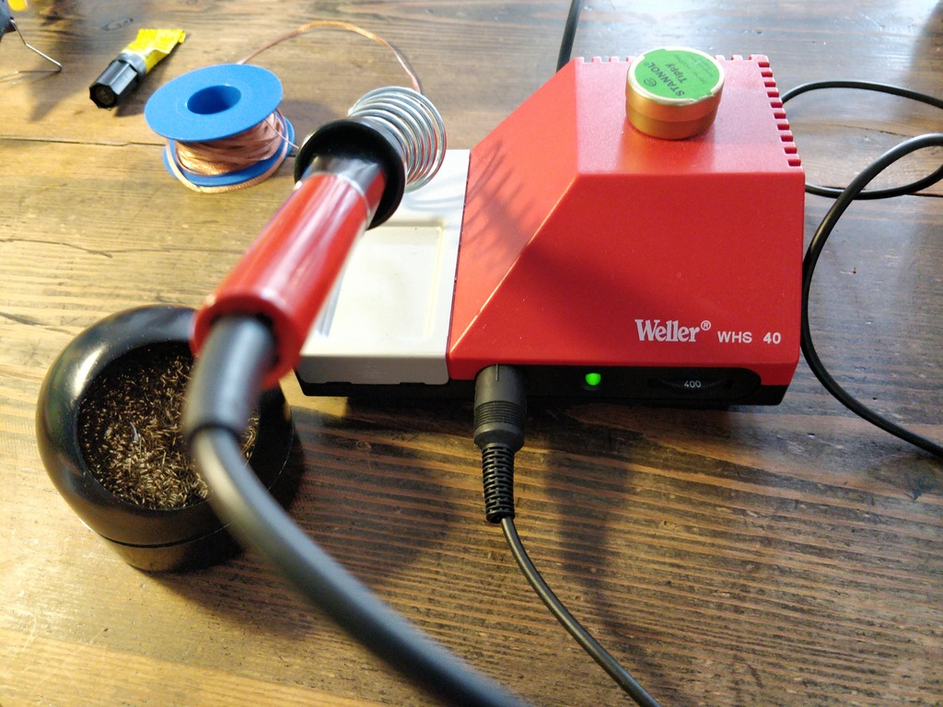
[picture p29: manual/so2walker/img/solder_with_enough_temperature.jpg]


****
Keep the electronic parts together as they are tiny and get lost easily when they are accidentally dropped from the table.
****

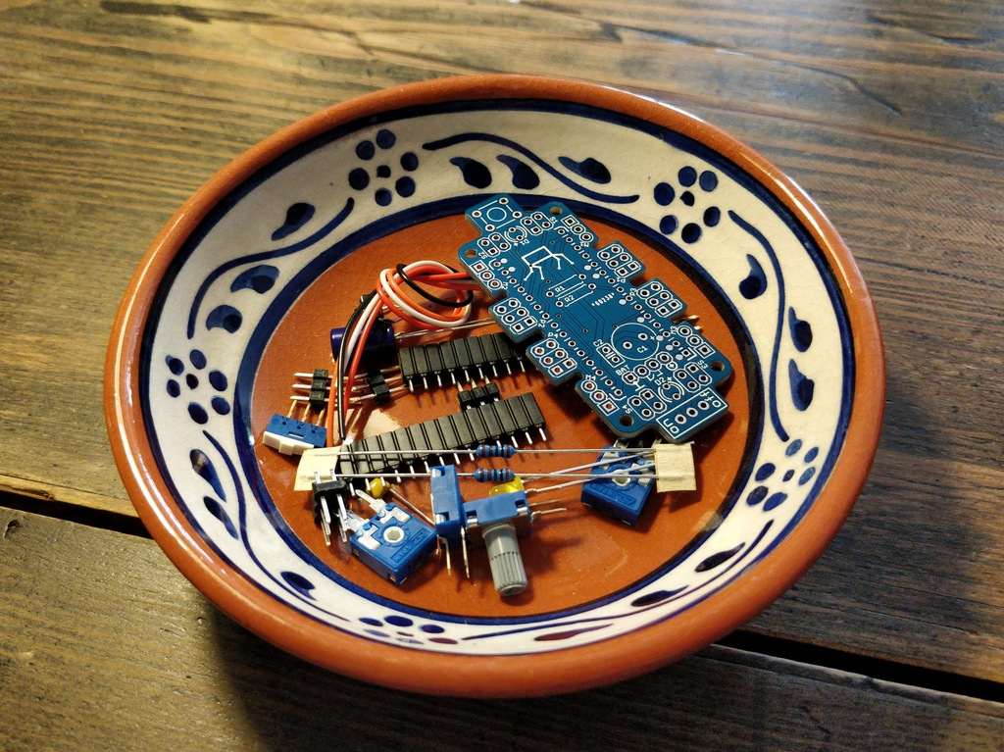
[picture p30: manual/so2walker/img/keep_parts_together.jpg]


=== Solder Nano-Board Header
****
So now you should be prepared for soldering the first part. Insert header pins for the _Nano-Board_ as shown in the picture.
****

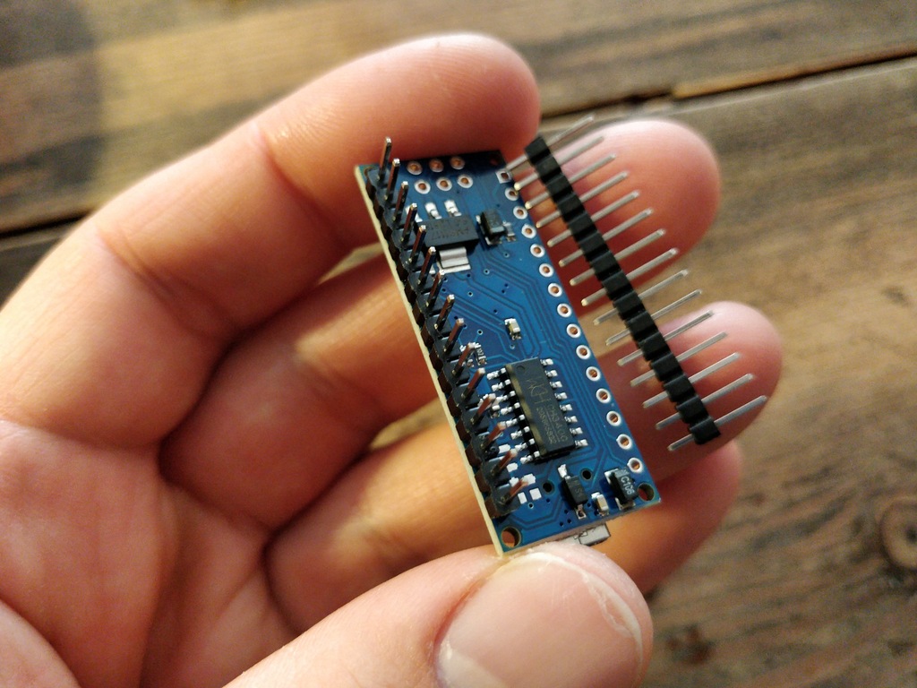
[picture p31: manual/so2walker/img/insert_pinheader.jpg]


****
You can use a breadboard, if available, for stabilizing the pin headers and keep them aligned and perpendicular during soldering.
****

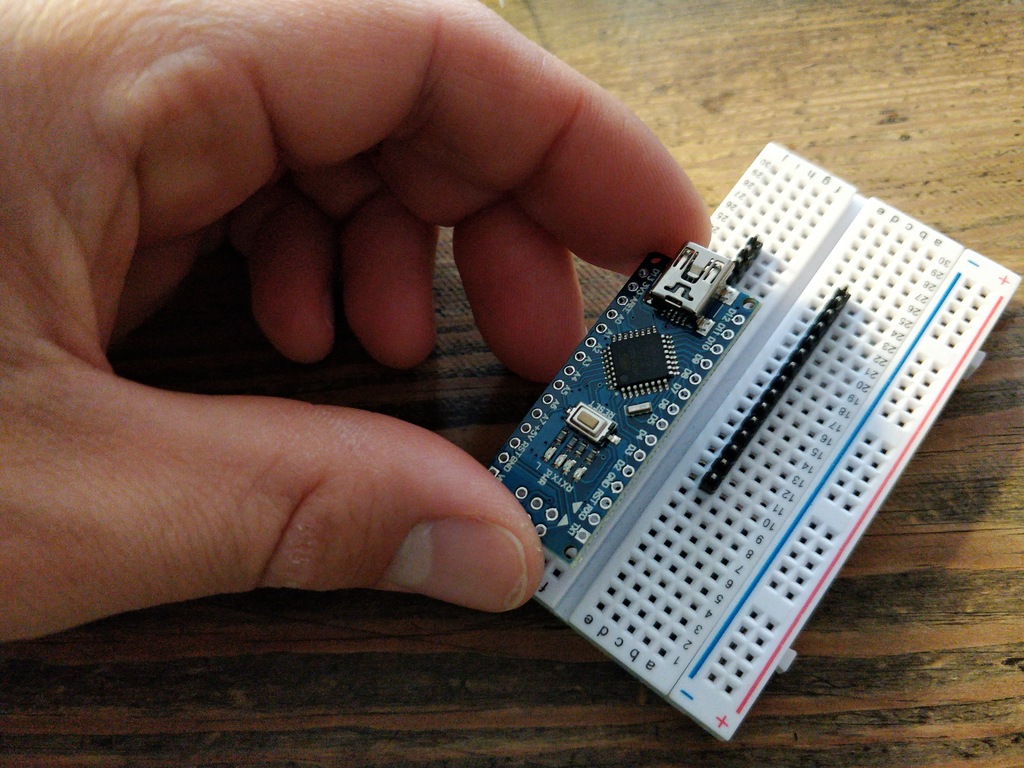
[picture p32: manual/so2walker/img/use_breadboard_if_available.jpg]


****
Solder the pins one after another. After soldering the first pin, double-check for alignment and correct it if needed. Otherwise, continue soldering all 30 pins.
****

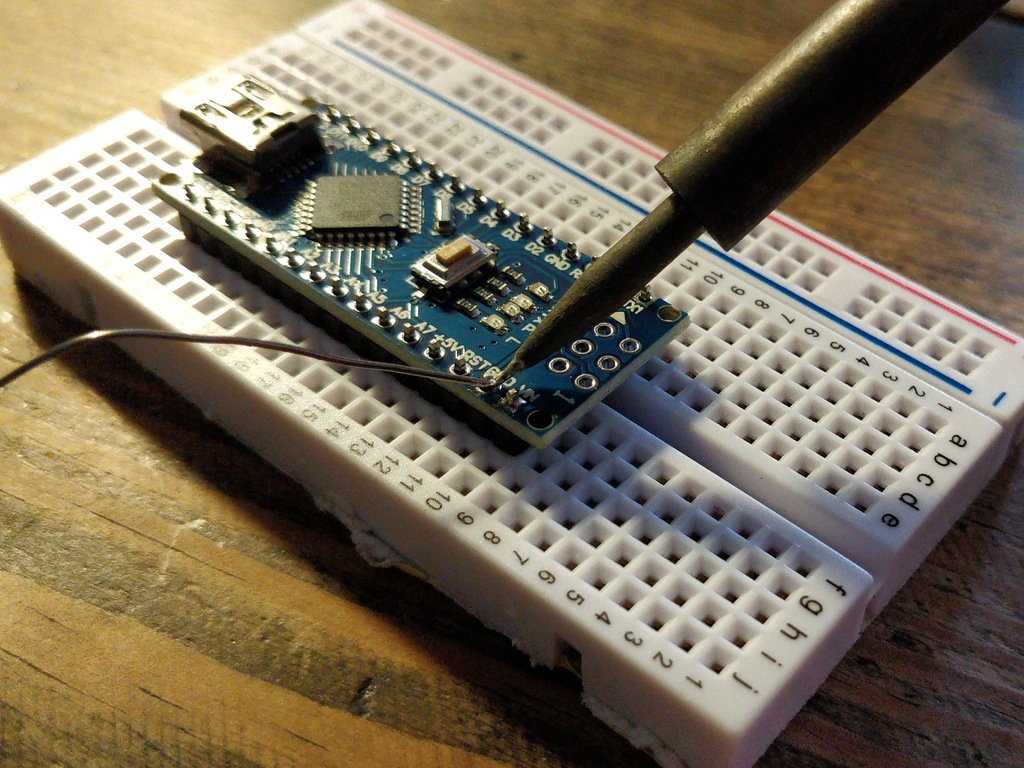
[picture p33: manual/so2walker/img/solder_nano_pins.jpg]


****
The result should look like this. Sufficient solder looks shiny and volcano-shaped. If it looks like a water drop or ball then there is too much solder. You can remove it by cleaning the tip and put the soldering iron again to the pin.
Alternatively, use de-soldering braid to remove excessive solder.

If the solder point has a weird shape or _noses_, then there was probably not sufficient flux available in the melting process, use a little _fresh_ solder to make the solder point shiny again.
****

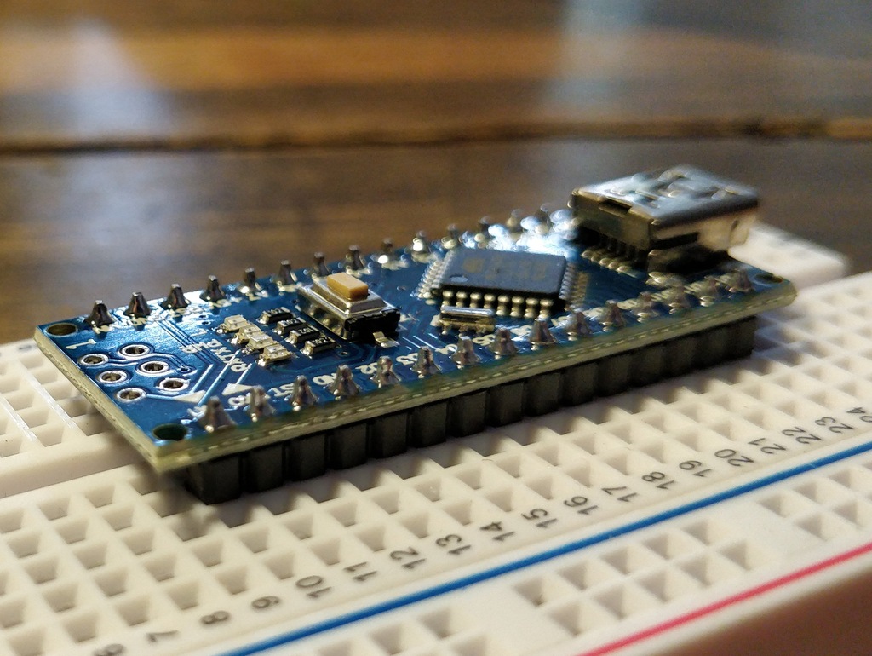
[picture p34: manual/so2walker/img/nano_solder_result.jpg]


=== Resistors

****
Get the two 1 Kilo-Ohms resistors and the motherboard. Don't get irritated as the color might be different than shown in the picture.
****

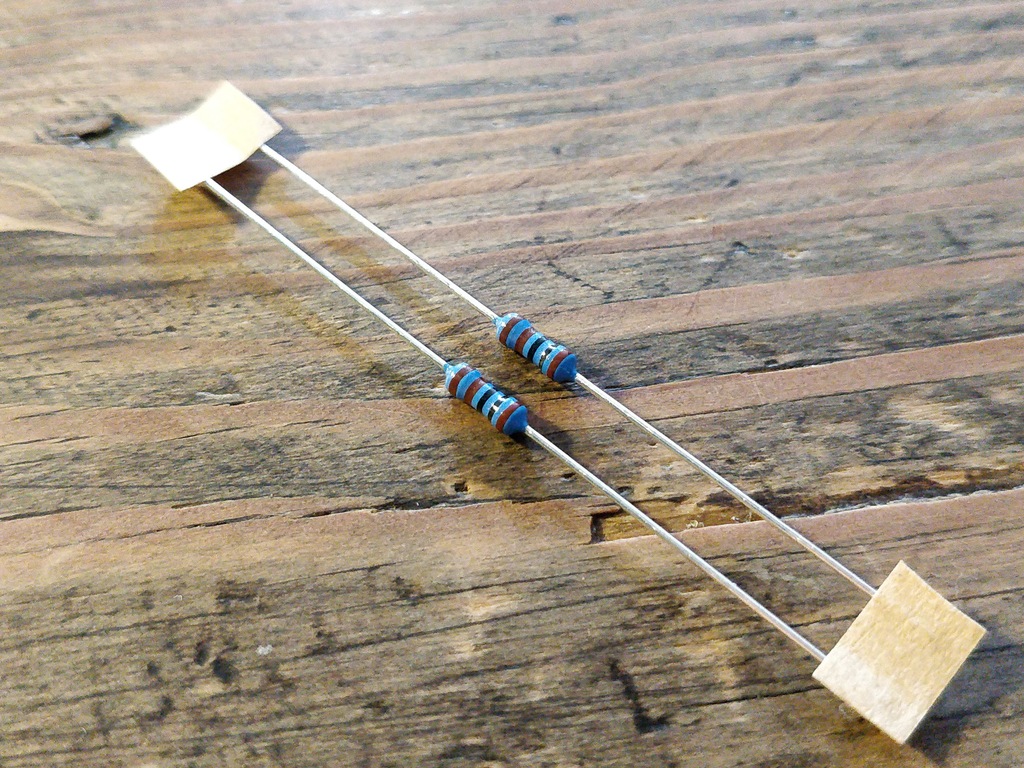
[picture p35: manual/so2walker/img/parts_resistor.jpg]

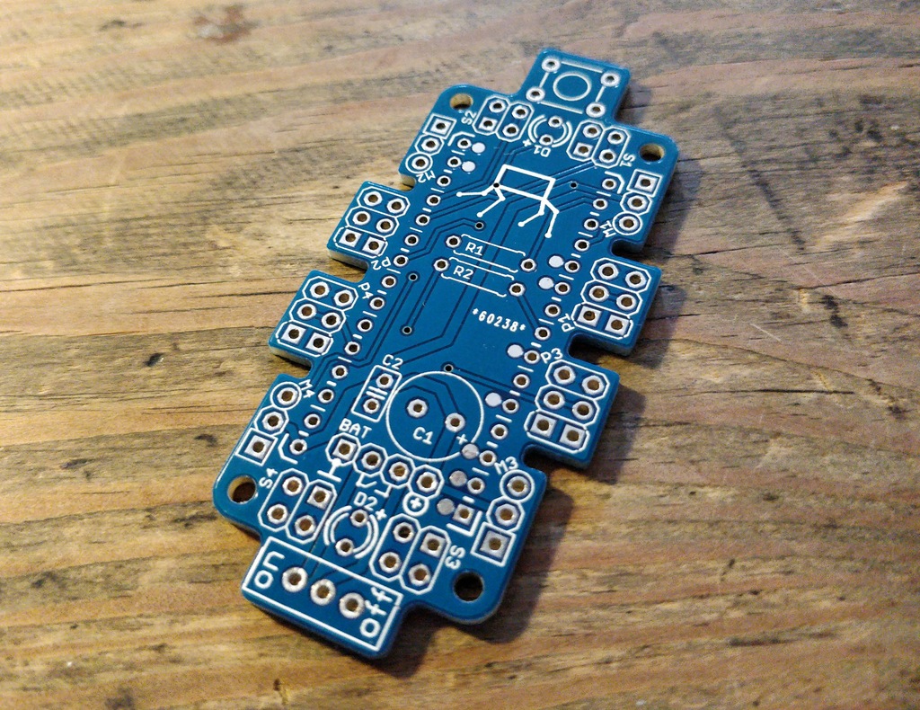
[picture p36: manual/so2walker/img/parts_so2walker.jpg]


****
Bend down the resistors' leads very close to their ends and trim the leads as shown in the picture.
****

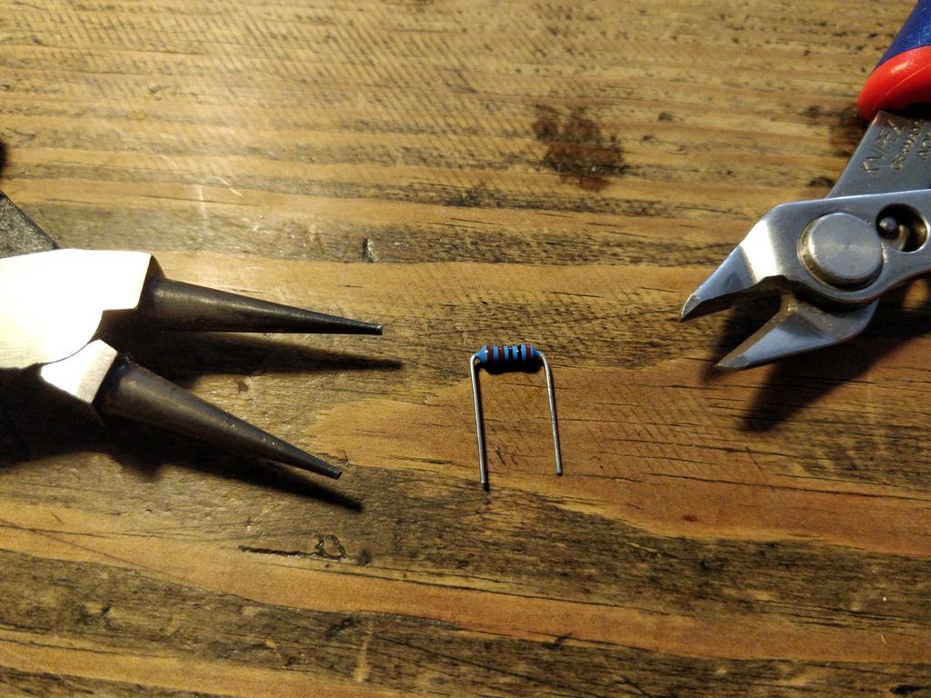
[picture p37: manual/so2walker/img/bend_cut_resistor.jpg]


****
Insert resistors as depicted and printed as R1 and R2 on the board's silk screen. Make sure that the resistors are soldered very closely to the board.
****

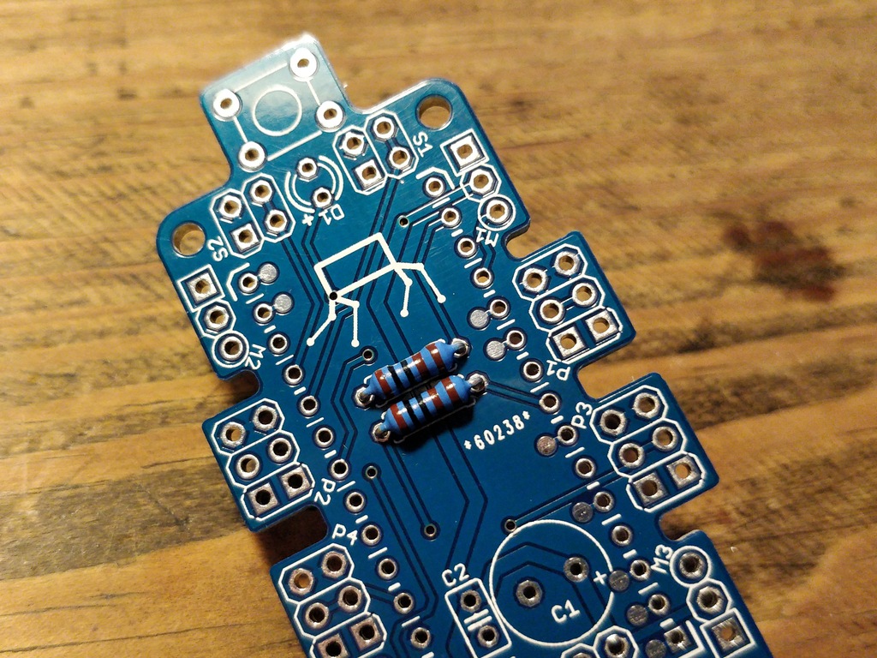
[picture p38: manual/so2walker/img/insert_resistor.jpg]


****
Trim the leads after soldering using the side-cutting pliers.
****

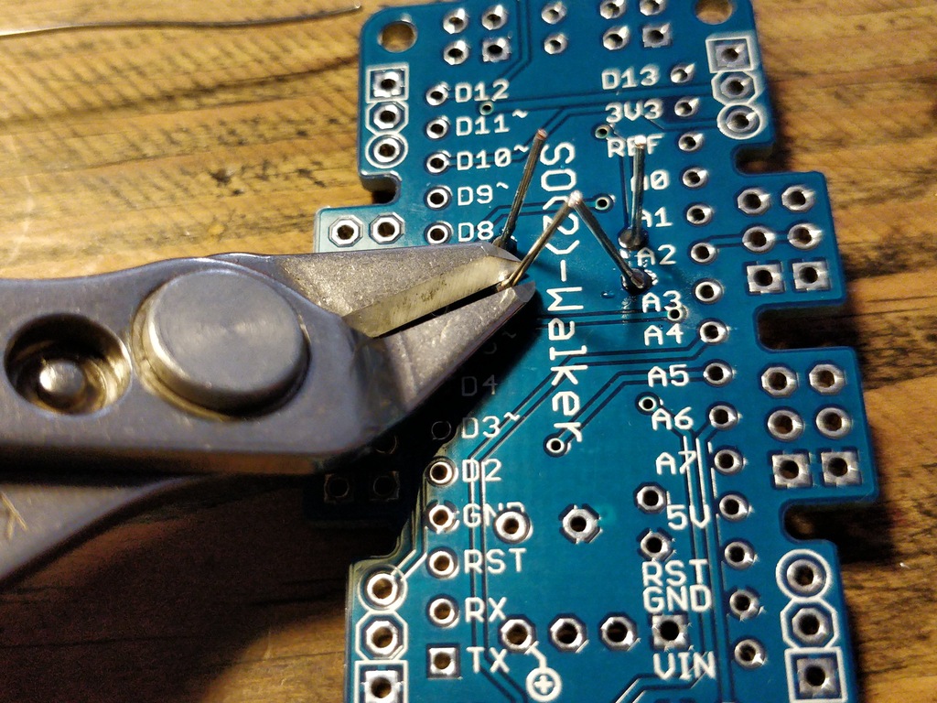
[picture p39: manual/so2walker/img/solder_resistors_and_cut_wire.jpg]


=== Capacitors

****
Get the two capacitors. They completely differ in size and form.
****

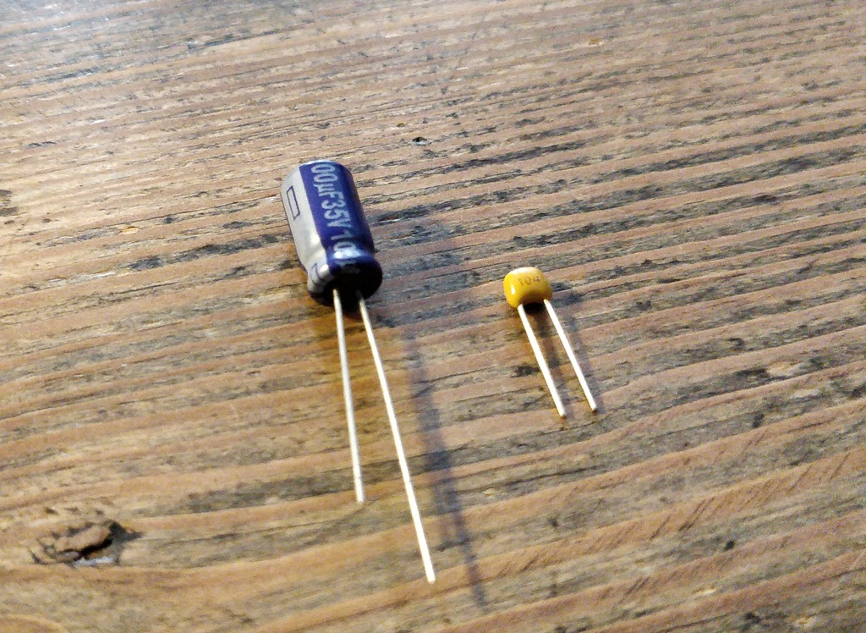
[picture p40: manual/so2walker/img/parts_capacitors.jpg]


****
Insert the ceramic capacitor (small) first as it has a lower profile. Again, make sure that the capacitor is soldered very closely to the board.
****

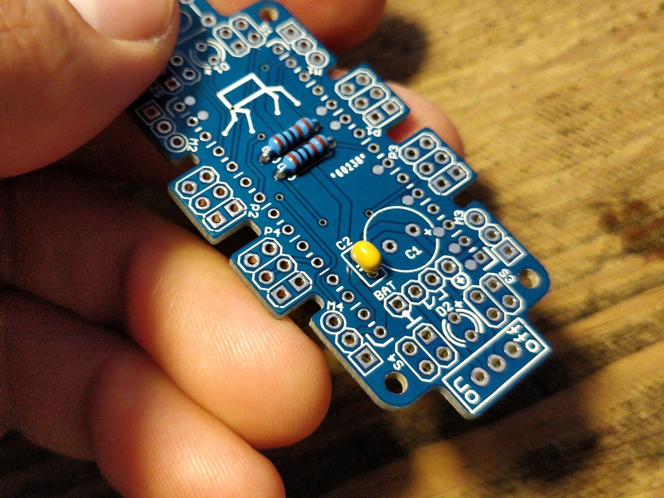
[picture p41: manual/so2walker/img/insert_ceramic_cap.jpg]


****
The electrolytic capacitor has a polarity and its leads must not be mixed up. The shorter lead is minus, the longer lead is plus. Make sure polarity is correct as denoted on the board and shown in the picture. The capacitor must be laid on its side since the _Nano-Board_ will be mounted above it.
****

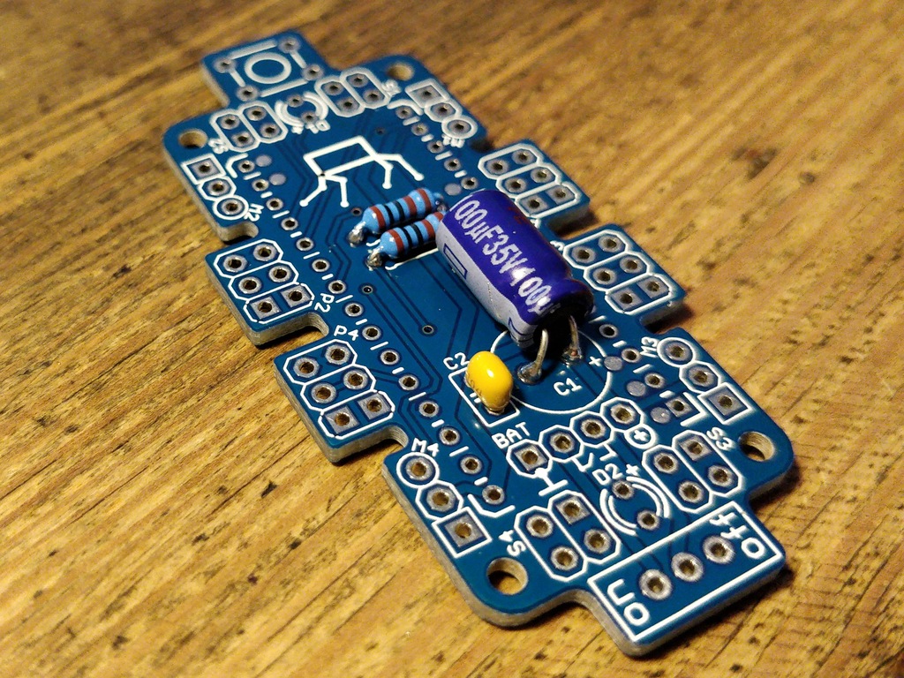
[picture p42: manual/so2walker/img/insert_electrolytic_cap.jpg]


=== LEDs
****
Get the LEDs. Their colors or shape can be different depending on the version of the assembly kit.
****

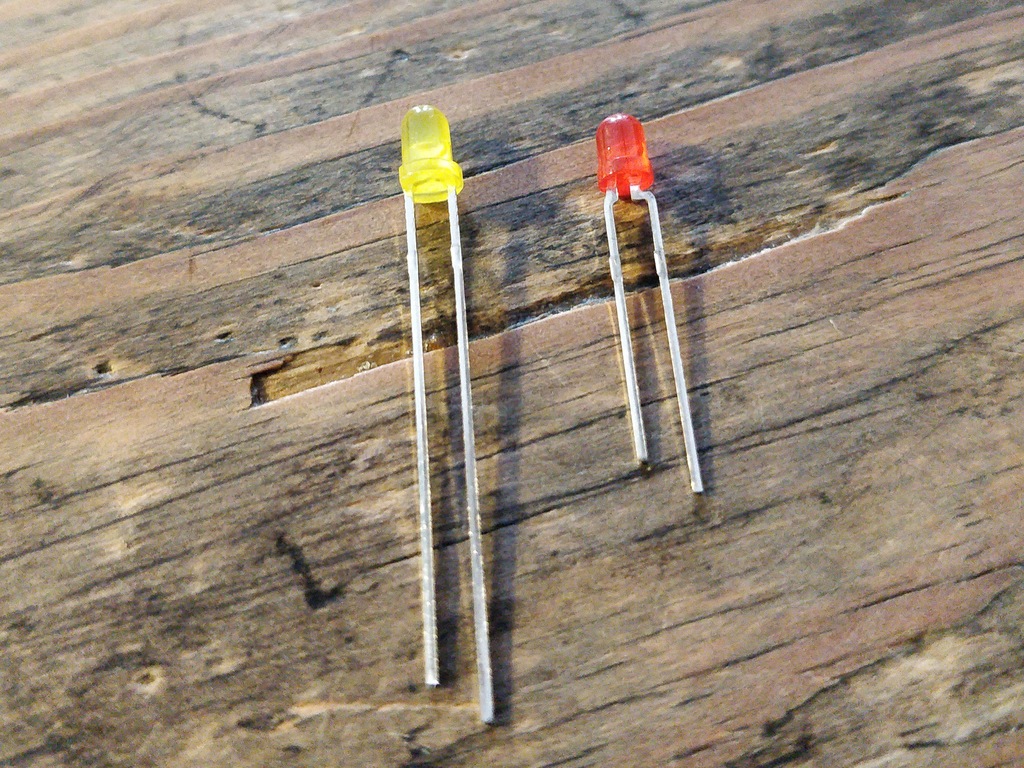
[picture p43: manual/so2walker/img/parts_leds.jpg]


****
The LEDs also have polarity. Again, the shorter lead is minus, the long lead is plus. Make sure polarity is correct as denoted on the board and shown in the picture.
****

NOTE: To remember which lead is plus or minus, imagine, there is a rule of thumb: The dashes of the plus sign put together in a line are longer than the minus dash. Easy, isn't it?

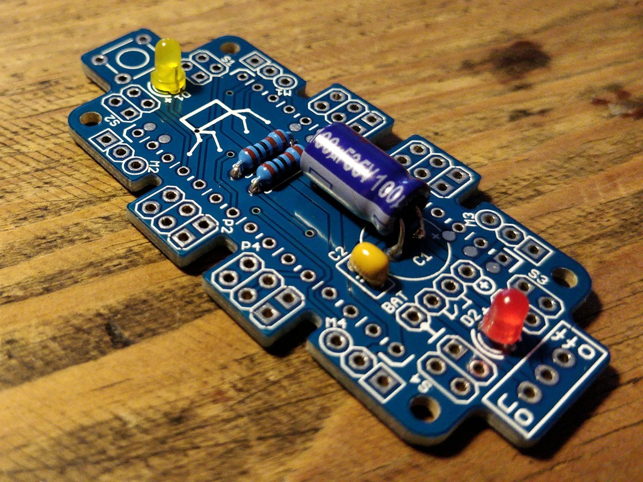
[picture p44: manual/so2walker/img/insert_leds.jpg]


=== Switches

****
Get the switches. The silver/black one is a tactile switch, a button so to say. The other one (blue/white) is a slide switch.
****

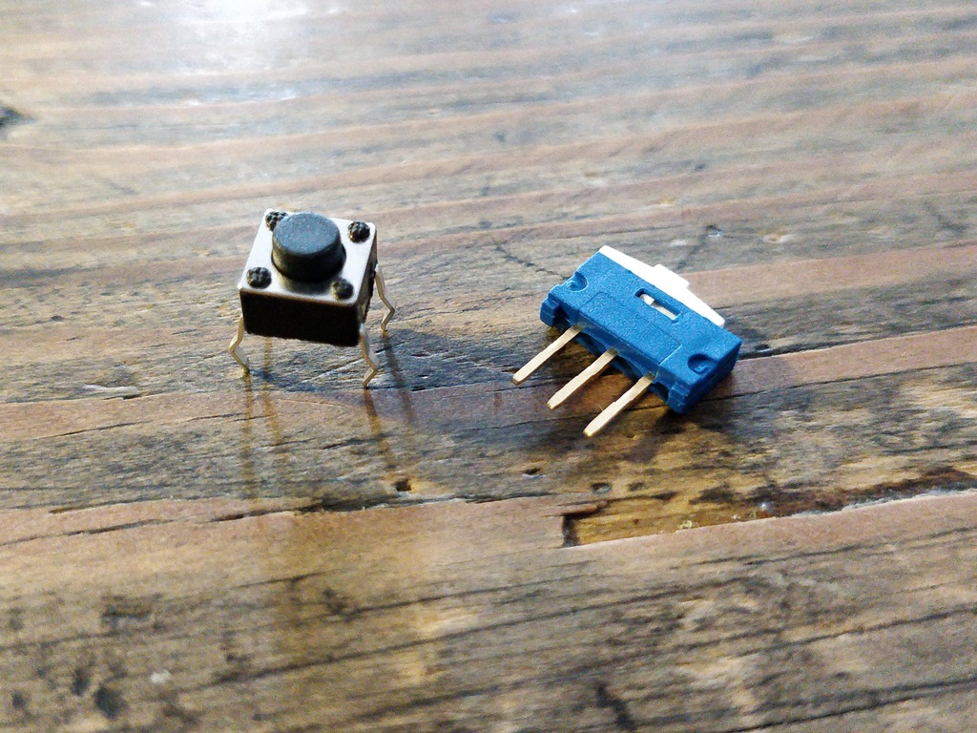
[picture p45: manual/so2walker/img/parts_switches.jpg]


****
Insert and solder the slide switch and button. When inserting the tactile button, look out for correct orientation. There is only one correct way and you probably need to gently press the part into the board. You feel a little click when inserted correctly. The orientation of the slide switch is pretty clear and can be installed in both ways. After soldering, make sure that the slide switch is turned off (as marked on the board).
****

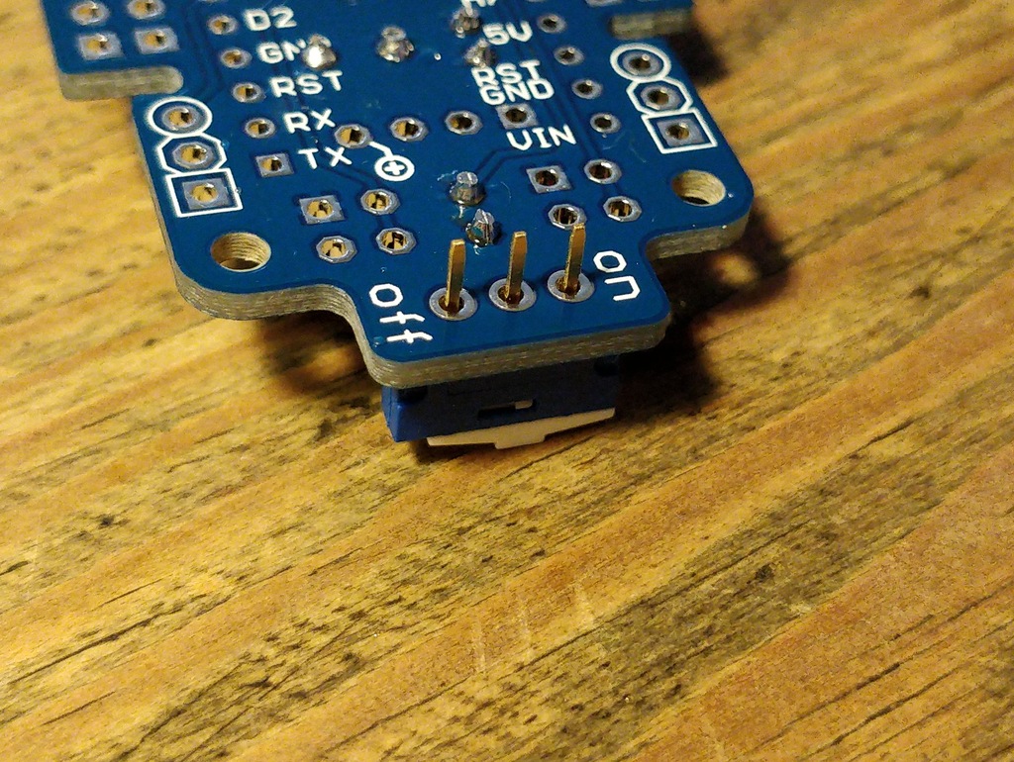
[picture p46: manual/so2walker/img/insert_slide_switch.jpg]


=== Socket
****
The next thing to solder is the sockets for the _Nano-Board_. The sockets in your package might have more than 15 slots, so you need to trim the socket to exactly 15 slots and use sanding paper to make it even. Be careful when trimming the sockets, they might break easily. You have to cut directly through the 16th socket pin, *not between pins* as this might accidentally break the 15th pin as well.
****

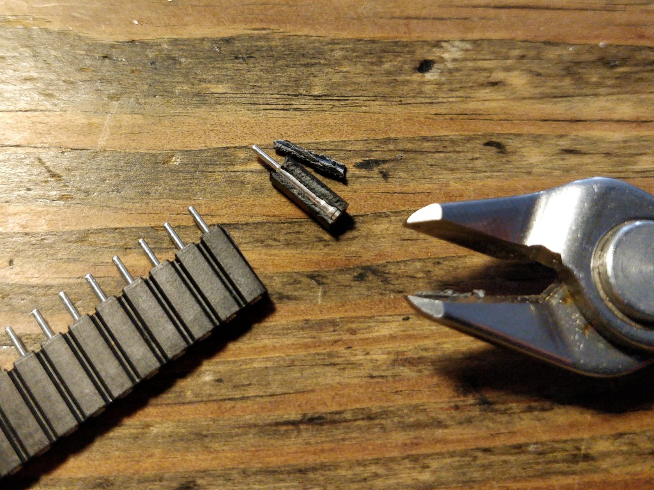
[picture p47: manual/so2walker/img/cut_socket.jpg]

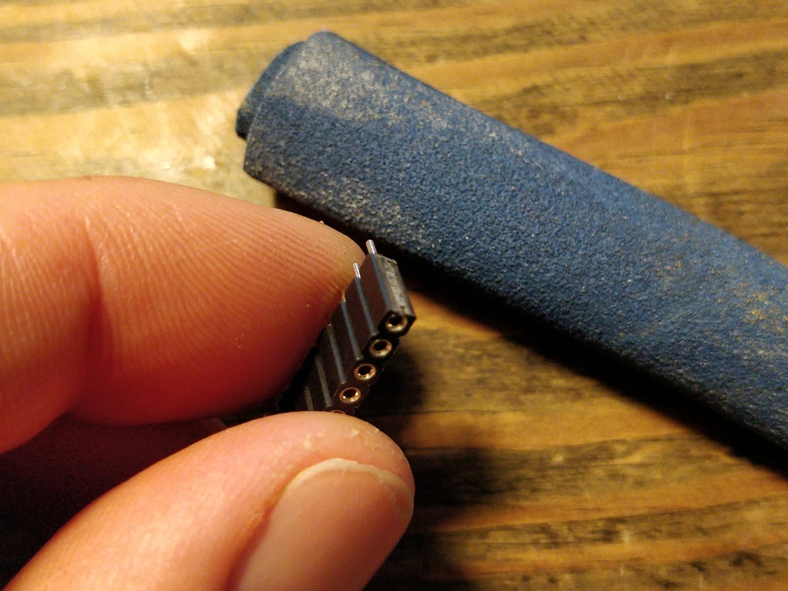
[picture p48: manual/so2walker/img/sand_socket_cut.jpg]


****
Then insert the socket and solder the 30 pins. For each half of the socket, make sure the sockets are aligned perpendicular and closest to the board. Otherwise, the _Nano-Board_ might not fit into the socket.
****

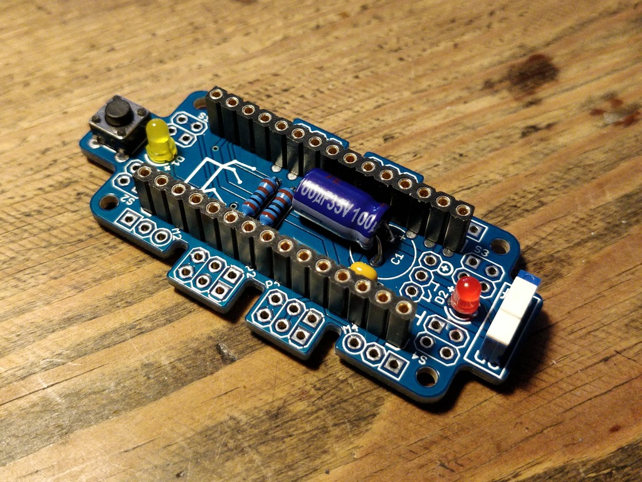
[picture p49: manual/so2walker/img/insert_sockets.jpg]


== Get a break

NOTE: Now it's time to grab a coffee or similar and relax your eyes. Get some fruit and fresh air, give your body a break :)

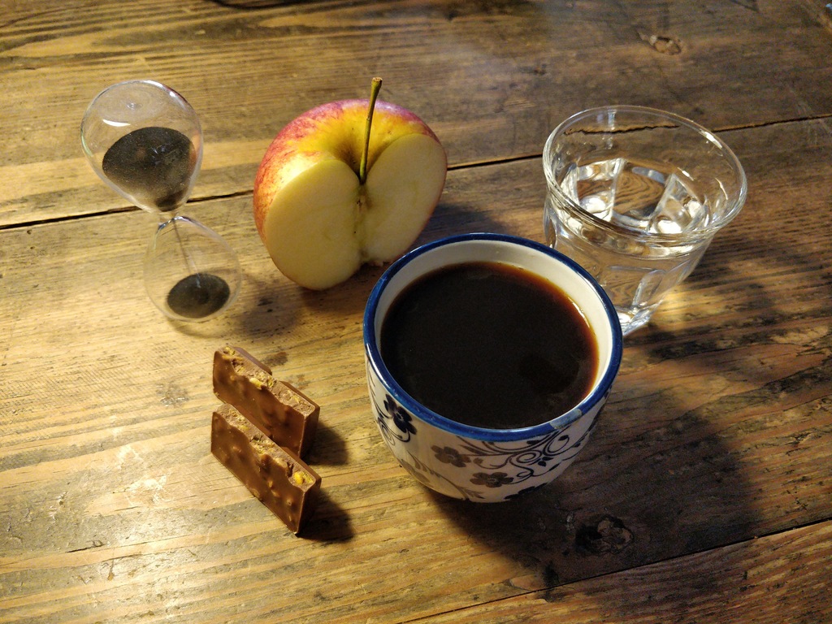
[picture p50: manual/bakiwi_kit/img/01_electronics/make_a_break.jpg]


== Soldering (continue)

****
Hope you are relaxed, now :)
****

=== Servo Header

****
Get the servo pin headers and insert four times the 1x3 pin servo header to all four corners of the board, next to the screw holes.
Again, make sure the pins are perfectly perpendicular to the board, otherwise, the servo connectors might interfere with the sockets of the _Nano-Board_.
****

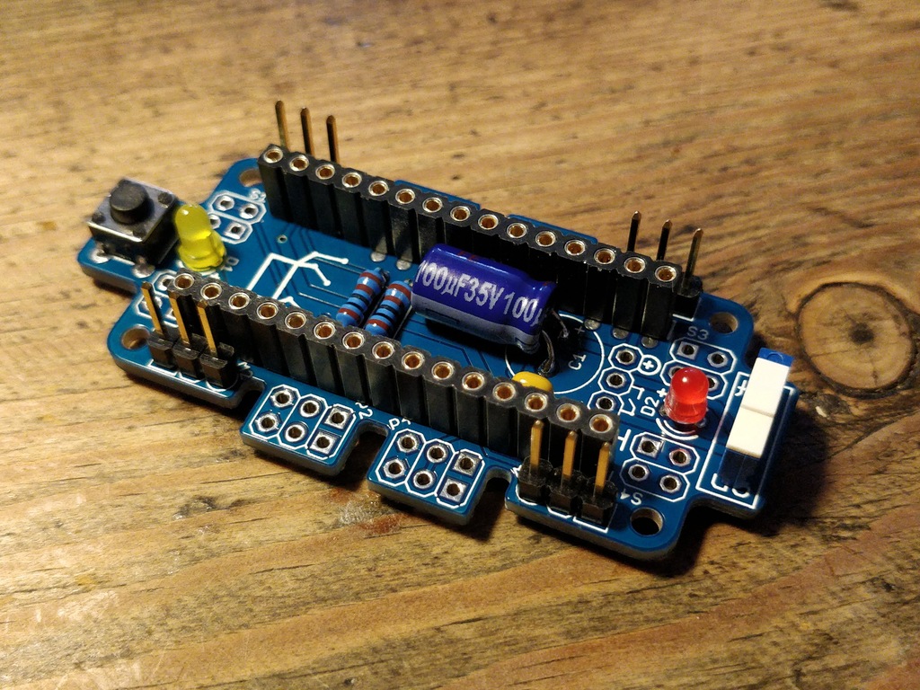
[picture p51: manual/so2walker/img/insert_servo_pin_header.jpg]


=== Potentiometers
****
Get the four potentiometers (10 KOhms) and the associated knobs (might have a different color) and insert the knobs in such a way that the shiny metal part of the potentiometer is on the back. When inserting the knobs, make sure the arrow is pointing upwards. Check for correct _neutral_ position (pointing to the top), e.g. when turned fully to the left end stop the arrow should point in the lower left corner and when turned fully to the right end stop, the arrow should point to the lower right corner.
****

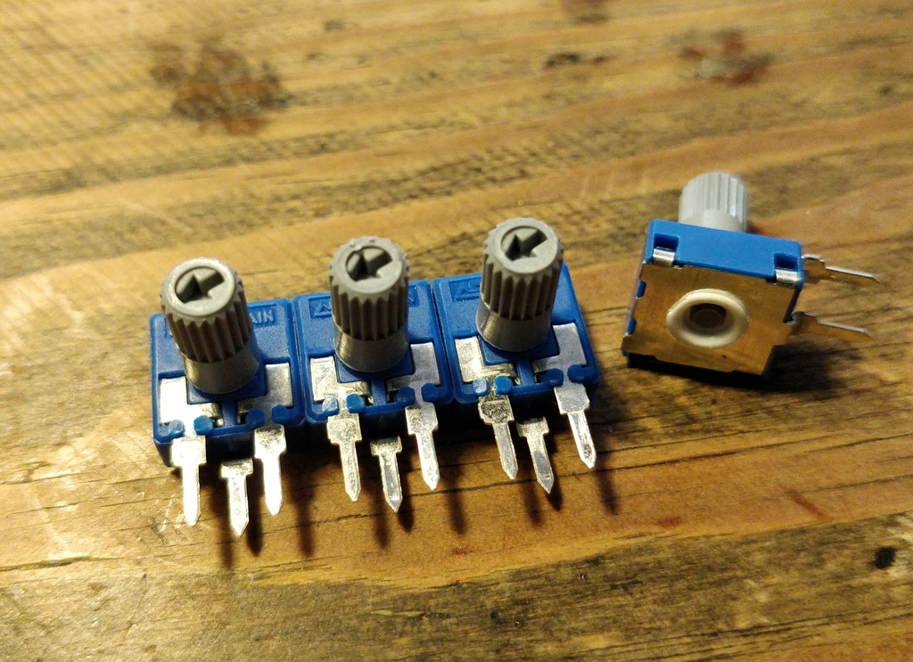
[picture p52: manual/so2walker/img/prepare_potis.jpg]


****
Insert the potentiometers as shown in the picture, turn the board and solder them.
****

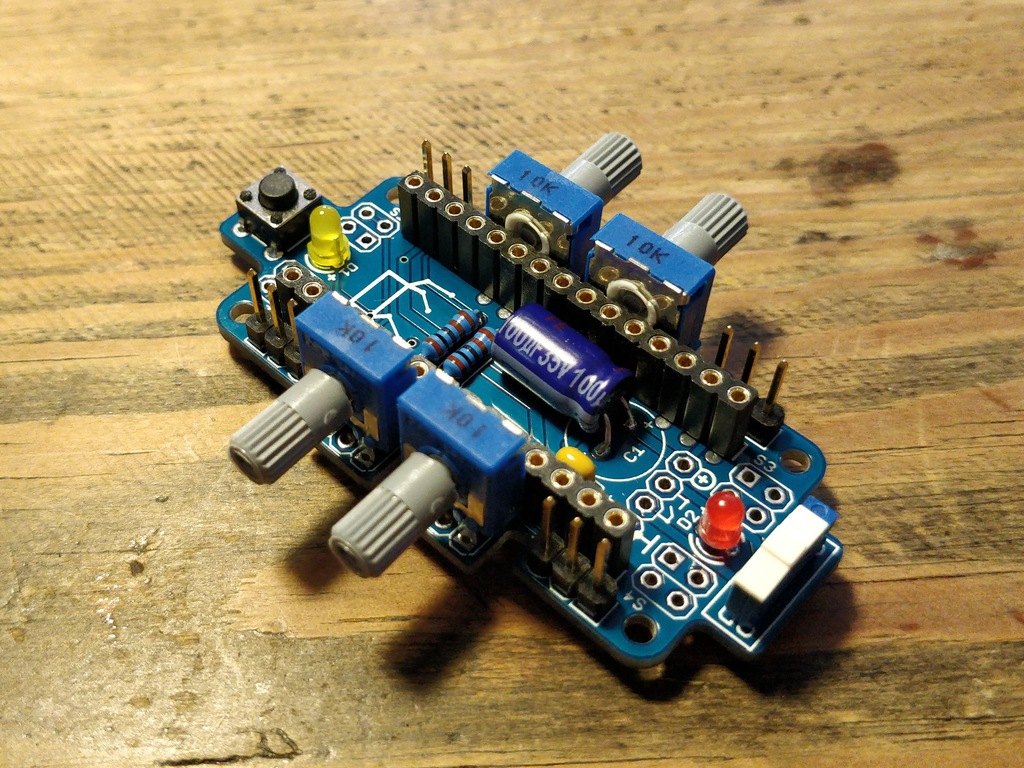
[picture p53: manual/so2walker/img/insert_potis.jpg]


=== Battery Pack

****
Get the wires (approx. 10 cm each). The might have different colors than depicted or the wires come as a flat cable.
****

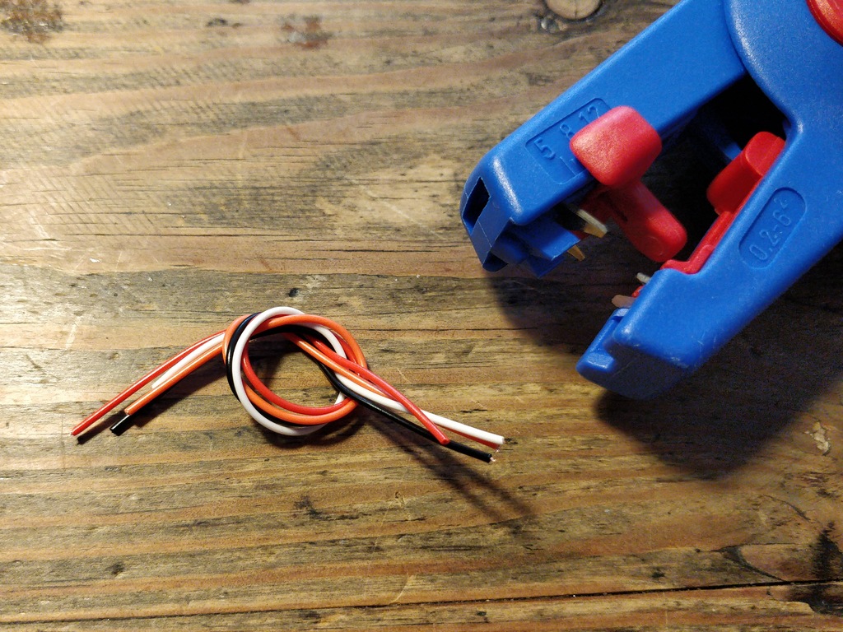
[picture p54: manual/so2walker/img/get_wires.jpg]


****
Strip the insulation of all the wires' ends, approx. 3-5 mm, twist the ends a little and pre-solder the wires. Pre-soldering is useful to better insert the wire into solder holes.
****

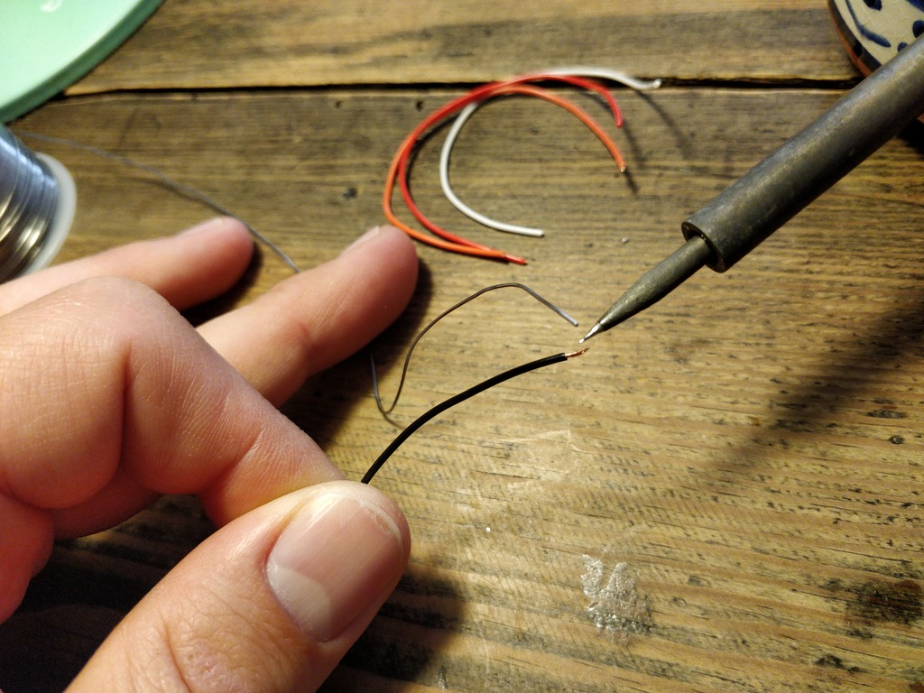
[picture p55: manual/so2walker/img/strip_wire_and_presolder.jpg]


****
The result could look like this.
****

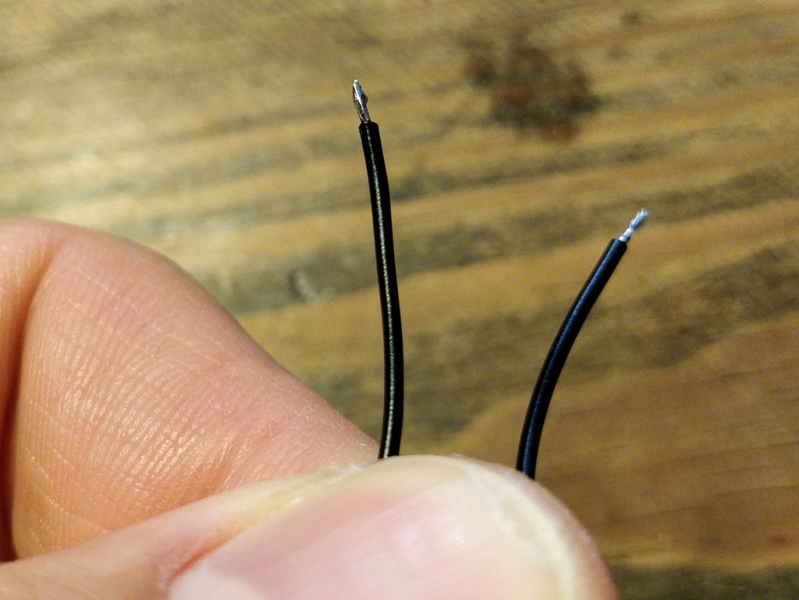
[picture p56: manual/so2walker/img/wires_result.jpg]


****
Insert the wires in the denoted order and solder them to the board.
****

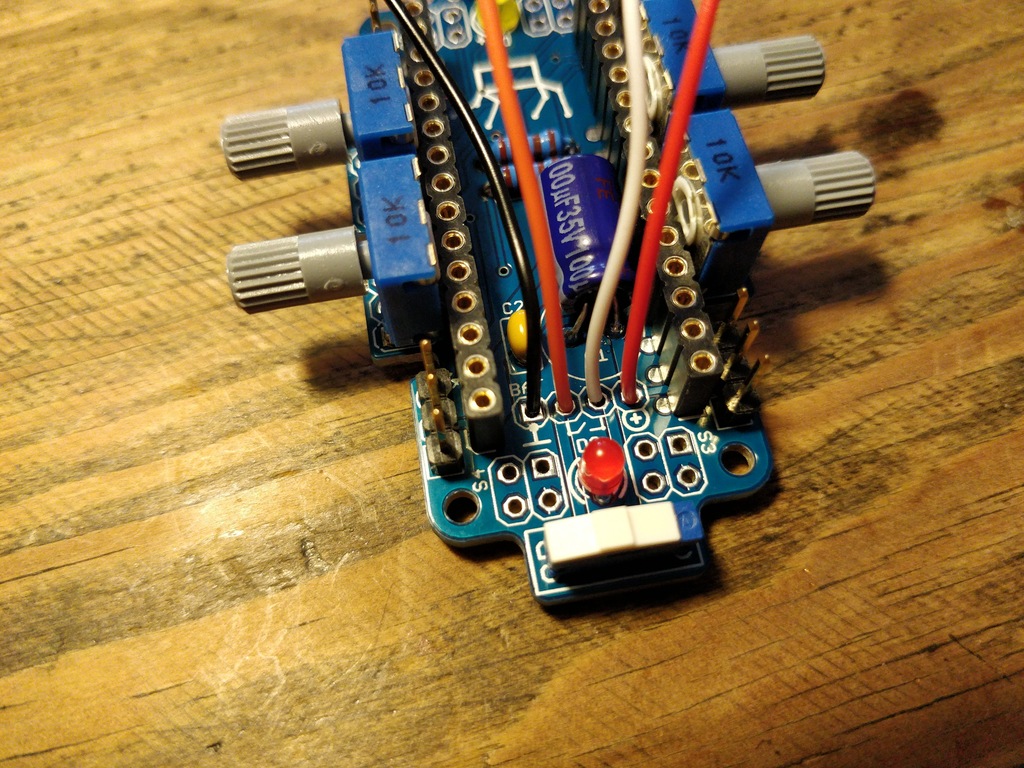
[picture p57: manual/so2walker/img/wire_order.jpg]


****
Twist pairs of wires, each pair will be associated with a single battery pack of two cells. If you have a flat cable, you can split them in two pairs of wire.
****

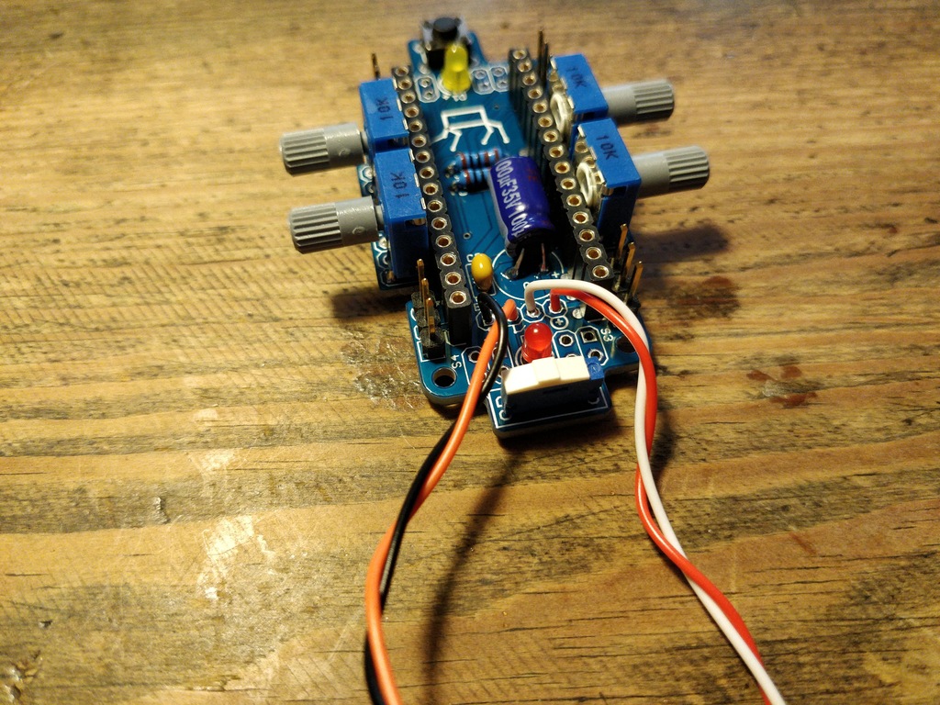
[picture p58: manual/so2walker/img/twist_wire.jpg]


****
Turn the leads of the battery pack a little upwards so they do not stick out over the part.
****

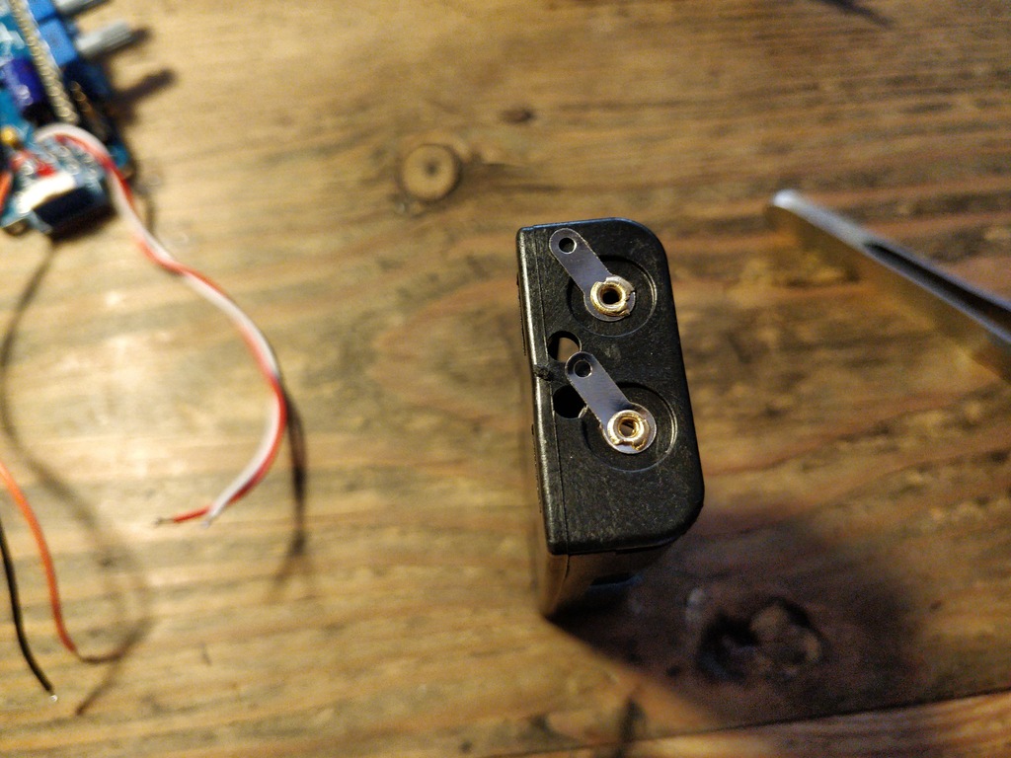
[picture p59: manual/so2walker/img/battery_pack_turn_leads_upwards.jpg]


****
Check polarity of the battery pack (it is denoted inside the packs).
****

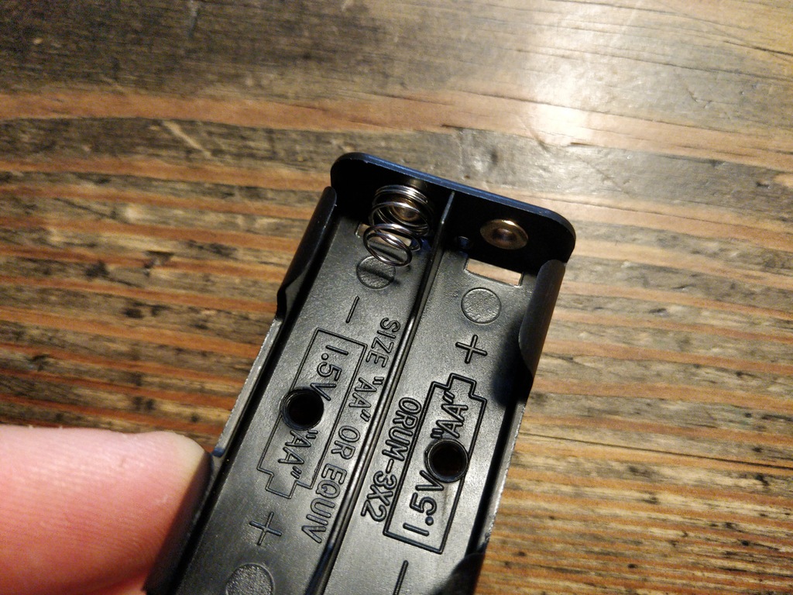
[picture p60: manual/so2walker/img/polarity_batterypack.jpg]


****
Solder wires to the battery packs as shown. Double check for correct polarity. According to your cable colors the order should be (B1- B1+ B2- B2+) with Bx denoting the battery pack (1 or 2), as denoted on the board/schematics.
****

CAUTION: Battery packs are made of temperature-sensitive plastic. Try to solder only as short as possible in order to avoid melting the plastic. This could irreversibly damage the pack and lead to connection problems later.

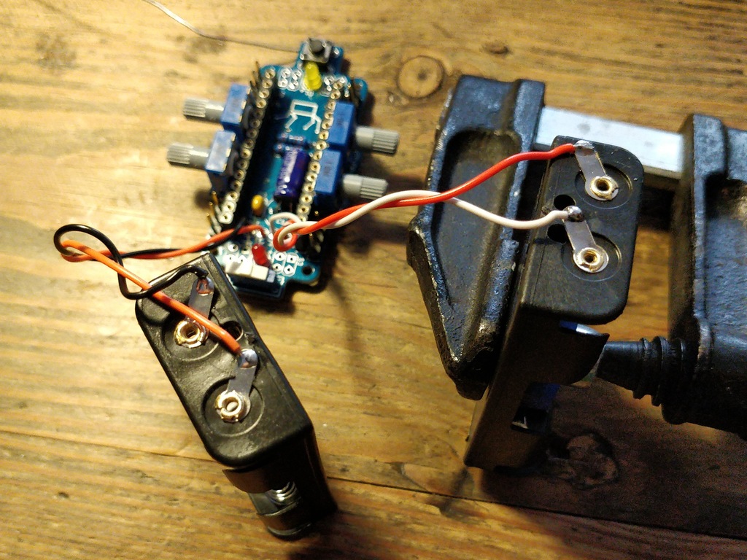
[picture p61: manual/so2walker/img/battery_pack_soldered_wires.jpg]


=== Soldering finishing

****
So, congratulations. You did it. You finished soldering. Yay. \o/

Next thing to do is to trim the pins to be as short as 1-1.5 mm.
****



****
Dispose the trash material correctly. Metal, plastic and paper parts can be recycled and should not be put to residual waste.
****



NOTE: Do not dump the bags. Re-use them or return them to your workshop leader if you do not need them anymore. Save resources. There is no planet B, right?



== Testing and Flashing Firmware



****
Before installing batteries, get your multimeter and check at least for three things:

* Use the short circuit detection mode (beep mode) and check whether there is good connection between the battery packs and the board. Measure from the very end (e.g. the spring in the pack) to the wire end soldered to the board. The multimeter should make a beep sound here signaling a proper (low-resistance) connection.

* Next check the four battery cable ends for possible cross connections. There should be none (if you nonetheless find a short circuit between the inner cables, make sure that the power switch is in _off_ position). Remove any short circuits.
Check (optically) for possible short circuits on all your soldered connections on the motherboard and _Nano-Board_. If unsure, check (electrically) with the multimeter.

* The last thing: Check electrically (!) for potential short circuits between GND, VIN and +5V as denoted on the _Nano-Board_ pins.

Please be careful with this last step and make sure that there is no short circuit (left) as this can destroy components of your robot irreversibly. In any case, if some component of your robot is getting hot, remove batteries immediately and check for potential problems. Maximally the motors are getting warm after longer use, the rest of the robot should stay at environment temperature.
****

=== Insert Batteries
****
Now it is time to first power-up your freshly soldered Bakiwi robot.

* Make sure the power (slide) switch is in "off" position.
* Insert the _Nano-Board_ into the sockets of the motherboard with the USB connector turning pointing towards the tactile switch.
* Insert all four batteries into the holders according to the polarity denoted inside the battery holders and the batteries themselves.

* Switch the power on and the _Nano-Board_ should be light-up its onboard LEDs.
****

=== Installing Arduino IDE
****
Get a computer and browse to link:https://www.arduino.cc/en/Main/Software[] and download and install the latest Arduino IDE according to the description on the Arduino website. If you already worked with Arduino boards and have the IDE already installed on your computer, you might consider updating to the current version as it might be required to detect the _Bakiwi_ robot's control board in the Arduino IDE. This manual was tested with version 1.8.8 without any problems or modification needed.
****

=== Checking out the Code-Repository
****
Download the latest _Bakiwi_ firmware source code folder with name *so2walk* from link:https://github.com/ku3i/Bakiwi.git[] and save to your local hard drive (hit the *Clone or Download* button on the _Github_ website).

Alternatively, if you are familiar to a _Linux_ terminal and want to use the source code version system _Git_, type
----
git clone https://github.com/ku3i/Bakiwi.git
----
to clone the code repository to your computer. Optionally, if _Git_ is not already installed on your _Linux_ machine, type
----
sudo apt install git
----

If you have question on using _Git_ (e.g. for other operating systems), please refer to link:https://www.git-scm.com/[].
****

=== Compile Firmware

****
Open the _Bakiwi_ firmware's source code in the Arduino IDE (file->open) and hit the _compile_ button (it looks like a checkmark, it's somewhere in the left upper corner). When compiling works without complains from the IDE then all the code dependencies seem to be fulfilled on your machine and the compiler was able to create the binary code to be run by the microcontroller on the _Nano-Board_.
The firmware source code file is located in:
----
Bakiwi/source/so2walk/so2walk.ino
----

****

=== Connecting the Nano-Board to a PC
****
Remove batteries again and connect the _Nano-Board_ to your computer via USB (mini)-cable. The board should immediately power-up again as you connect the cable.
****



=== Selecting Board and Microcontroller
****
Next you need to select the target board and processor. The _Nano-Board_ is compatible to Arduino Nano and hosts an 8-bit ATMEGA328p microcontroller. After setting the board via _Tools_ -> _Board_ -> _Arduino Nano_ you also have to select the correct microcontroller and Bootloader combination via _Tools_ -> _Processor_ -> _ATMEGA328P (Old Bootloader)_. If the _old-bootloader_ option is not available in your Arduino IDE you may consider updating to the current version.

Please note: The board uses an USB-to-Serial chip-set called "CH340" which, depending on your operating system, may need some sort of driver to be installed.
****



=== Uploading Firmware
****
You can now upload the code by hitting the _upload_ button (an arrow to the right). If everything has worked out fine, the motherboard's LEDs should blink in a periodic pattern.
****

=== Testing the Functions
****
For testing, follow these steps:

* remove the USB cable
* make sure robot is switched off
* connect motors (yellow cable pointing towards the knobs)
* insert batteries
* check all knobs are in neutral position
* switch on

The LEDs should again be blinking periodically. The four knobs modify the properties of the neural oscillator: Frequency, Phase and Amplitude (2x).

There are four 3-pin headers that allow for connecting motors. In the current version of the code only two of them are sending motor commands (the two next to the USB connector). The others you can use for connecting additional motors or sensors, when you modify or extend your robot or its code.

You find the knob which modifies the _frequency_ in the right upper position when holding the board with the USB connector upwards while looking from the _Nano-Board_ side. Try out modifying the frequency and watch the LEDs blinking accordingly. The blinking LEDs corresponds to moving motors later. So the motors will change direction with the same frequency as shown by the LEDs.

For each motor the oscillation is tapped at two different positions, so that you can create patterns that are either more _in-phase_ or _anti-phase_. The right lower knob modifies the _phaseshift_ between those taps. Try out the phase knob and so how you can create different blinking patterns.

When powering-up, your _Bakiwi_ is in _pause_ mode. You can now start the motors by hitting the tactile button. The motors will now begin to move according to the frequency and phaseshift you set.

The other two knobs (on the left side) can be used to modify each motor's amplitude. You can either decrease the amplitude by turning them to the right until the motors fully stop or you can increase the amplitude to a certain maximal value by turning them to the left.

Please note that a mixture of large amplitude _and_ high frequency at the same time can probably not be accomplished by the motor since every physical device has some sort of inertia.
****


== Assembly
****
We're sorry. The assembly manual for the development version of Bakiwi ("SO(2)Walker") ends here. How you create your robot's body is at the moment up to you for this version. However, the given pictures suggest how you can proceed. Try fixing the motors with double-sided tape first and try mounting them in some different angles. If you've found a working (and walking) solution then you may use permanent glue to attach the battery packs to the motors. The board can either by temporarily mounted with a rubber band or fixated with hot glue. Also using the surplus screws inside the motors' packaging is an option.

Let us know which solution works best for you.

****




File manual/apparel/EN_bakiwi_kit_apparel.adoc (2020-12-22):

=  Bakiwi Apparel Sewing Instructions
Doc Writer <kubisch@informatik.hu-berlin.de>
v0.1, 2020-12-16
:toc:
:toc-placement!:
:toc-title: Contents
:imagesdir: ./img/
:favicon: ../bakiwi_kit/img/icons/favicon.png
:stylesheet: ../bakiwi_kit/bak.css
:linkattrs:

:numbered:
:numbered!:

:icons: image
:icontype: png
:iconsdir: ../bakiwi_kit/img/icons/

ifdef::env-github[]
:tip-caption: :bulb:
:note-caption: :information_source:
:important-caption: :heavy_exclamation_mark:
:caution-caption: :fire:
:warning-caption: :warning:
endif::[]

:tip-caption: 💡
:important-caption: ❗
:note-caption: 📝
:caution-caption: 🔥
:warning-caption: ⚠️

_Instructions, templates and photos by Karen Ellenmeyer_



toc::[]

== Preparation
You will need the following tools and materials to tailor Bakiwi clothing:

=== Tools
* sewing machine (recommended)
* punch pliers
* sewing needle
* pins
* scissors
* pencil
* tape measure or ruler

=== Materials
* pieces of fabric with _light stretch_
* yarn
* all purpose glue

[TIP]
====
If you have no sewing experience at all, take a look at a few tutorials on the Internet or let friends or relatives show you some sewing, or ask if they can teach you how to use the sewing machine.
====

== Create the template
Create a cutting template by either sketching the given drawing on paper yourself or printing out the link:stencil/cut_stencil.pdf[template (PDF)] on paper or foil. If you have a 3D printer, you can also 3D print our link:stencil/cut_stencil.stl[stencil]. The dimensions given are for fabrics with _light stretch_.

[IMPORTANT]
====
The specified cutting templates and dimensions are made for fabrics with slight stretching (blue solid line). If you want to use very firm fabrics without noticeable stretching, we recommend making the template approx. 7 mm larger all around (dashed outer line).
====




== Fold the fabric and mark the cut
Fold the fabric so that the right sides (fur) are on the inside and the wrong sides are on the outside. Make sure the material's most stretch is is in cross direction. If you are using fur-like fabrics, make sure that the direction of the hair is facing down, i.e. that it can be smoothed towards the hem.

Put on the cutting template and mark the pattern with a pencil or chalk on the wrong (i.e. inner) side of the fabric. Don't forget to mark the positions for the sensors, too!




== Cut out the fabric
Pin both layers together with a few needles so that they can't move whilst cutting. Cut them out on the line, both at the same time, and as precisely as possible.




== Punch holes and reinforce
Use punch pliers to cut holes for the sensors through both layers of fabric. For best results when punching, put a piece of cardboard below, between fabric and support surface. then the holes can be cut out nice and clean.

Now secure the holes from fraying with a little glue. All-purpose glue should suffice. Use a needle or toothpick to gently spread the glue around the holes in a 3-4 mm radius. Let the glue dry long enough.




== Sewing

Sew around the edges foot width on your sewing machine. Make sure beginning and end are locked by sewing a few stitches back and forth.



== Turn the hem up and fasten it
Fold the hem 2 cm up and sew it by hand, going over the edges with double thread (_overlock stitch_). Alternatively, simply glue the hem all the way around. Make sure not to overuse the glue so it can’t bleed through to the right side of the fur.




== Try on
Turn over your newly created fur and dress up your Bakiwi. The feelers should first be inserted through the holes in the fur.

*Done!  Tadaahhhh.*

If you like, please be so nice and send us a photo or a video of your creation to *info@jetpack.cl* for our collection or post your individual Bakiwi apparel with the hashtag *#bakiwi*.




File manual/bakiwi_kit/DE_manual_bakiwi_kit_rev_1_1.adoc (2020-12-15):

=  Bakiwi Kit Bauanleitung
Doc Writer <kubisch@informatik.hu-berlin.de>
v0.21, 2020-12-15
:toc:
:toc-placement!:
:toc-title: Abenteuer-Verzeichnis
:imagesdir: ./img/
:favicon: {imagesdir}icons/favicon.png
:stylesheet: bak.css
:linkattrs:

:numbered:
:numbered!:

ifdef::env-github[]
:tip-caption: :bulb:
:note-caption: :information_source:
:important-caption: :heavy_exclamation_mark:
:caution-caption: :fire:
:warning-caption: :warning:
endif::[]



////
TODO 💡
	+ F.A.Q. / Troubleshooting
	+ find nice soldering tutorial
	+ describe schematics, boardlayout
	+ add to each part an explanation, schematics vs. pcb, vs symbol
////

toc::[]

:imagesdir: ./img/01_electronics/

== Vorbereitung

=== Werkzeuge
Für das Löten der Bakiwi-Elektronik benötigst du folgende Werkzeuge:

* Lötkolben (oder Lötstation) mit dünner Lötspitze
* Lötzinn (empfohlen: Dicke 0.5--0.75mm mit integriertem Flussmittel, bleifrei)
* Messingwolle mit Behälter ("Trockenreiniger"), alternativ ein angefeuchtetes Schwämmchen
* Seitenschneider oder Knipszange
* Multimeter (optional)




[NOTE]
====
Falls du noch gar keine Erfahrung im Löten hast, dann empfehlen wir dir, vorher ein Einführungsvideo oder Tutorial anzuschauen um schon mal eine ungefähre Vorstellung vom Löten zu entwickeln. Noch besser ist es, wenn du den Bausatz mit jemand anderem zusammen aufbaust, der bereits ein wenig löten kann.
====

=== Bauteile sichten
Überprüfe alle Bauteile auf Vollständigkeit. Zusätzlich zu den gezeigten Teilen hast du vielleicht Material beiliegen, welches sich für die Fühler deines Bakiwi eignet, z.B. Gitarrensaiten oder Pfeifenputzer.
// Tabelle mit Bauteilen



Lege alle Kleinteile in ein Gefäß, damit dir keines verloren gehen kann. Nimm dir zuerst die Bakiwi-Platine und leg sie vor dir hin. Die _Oberseite_ der Platine ist die mit den Bauteilbeschriftungen. Alle Bauteile werden nun nach und nach in einzeln erklärten Schritten auf der Oberseite eingesteckt und auf der _Unterseite_ festgelötet. Die beste Übereinstimmung mit den Bildern dieser Anleitung hast du, wenn du die Platine so drehst, dass du den `Bakiwi`-Schriftzug lesen kannst und sie mit der Beschriftung `POWER` zu dir gedreht ist und `PAUSE` nach oben zeigt.




Schalte die Lötstation ein und überprüfe die Temperaturanzeige. Wenn die Temperatur einstellbar ist, stelle sie passend zum Legierungs-Mischungsverhältnis deines Lötzinns ein (Aufschrift beachten). Wenn du dir unsicher bist, beginne mit 330°C, abhängig von der Leistung der Lötstation ist vielleicht eine etwas höhere Temperatur nötig. Wenn sich das Löten _klebrig_ anfühlt, dann kann die Temperatur zu niedrig sein. Erhöhe bei Bedarf die Temperatur allmählich, bis das Lot mühelos schmilzt.

// Was ist die maximale Temperatur? jenseites von 360° gibts doch eigentlich nix sinnvolles, oder?

[TIP]
====
Wenn deine Lötspitze auch bei stetigem Säubern nicht mehr glänzt und immer wieder dunkel wird ist die Temperatur vermutlich zu hoch eingestellt.
====

=== Nimm dir Zeit!

Das Zusammenlöten deines Bakiwis erfordert Ruhe und Konzentration. Die benötigte Zeit ist von Mensch zu Mensch unterschiedlich und sehr vom Vorwissen abhängig. Absolute Neulinge sollte 2 Stunden für das Löten einplanen, Profis schaffen das mitunter in 30 Minuten.

:numbered:
== Die Bauteile einlöten

=== Widerstände
Nimm dir die Widerstände zur Hand. Es gibt _einen_ blauen Widerstand und _zwei_ in beige. Beginne damit, das Papier an jeweils beiden Enden des blauen Widerstands abzuziehen.




Nun biege die beiden Draht-Enden mit deinen Fingern direkt an ihrem Ursprung um, sodass sie beide in dieselbe Richtung zeigen und sich die beiden Drähte parallel gegenüberstehen. Der blaue Widerstand hat die Bezeichnung `R3`. Suche nach dem abgebildeten Widerstandssymbol auf der Platine, es befindet sich unmittelbar unter dem `Bakiwi`-Schriftzug. Setze ihn wie auf dem Bild gezeigt auf der Platine ein. Ein Widerstand besitzt _keine_ Polarität, es spielt also keine Rolle, wie herum du diesen einsetzt.




Halte das eingesetzte Bauteil mit den Fingern fest, drehe die Platine vorsichtig um und leg Sie vor dir ab. Beginne nun damit, die Drahtenden auf der Platinenunterseite festzulöten. Achte dabei darauf, den Draht und die Lötfläche um das Loch gleichzeitig zu berühren und  aufzuheizen während du das Lötzinn hinzufügst. Die Wärmeübertragung funktioniert am besten, wenn die Lötspitze kurz vorher gereinigt und schon etwas mit Zinn benetzt ist.




Entferne den überstehenden Draht, indem du ihn mit einer geeigneten Zange (z. B. Seitenschneider) abknipst. Entferne dabei den Draht möglichst knapp über deiner Lötstelle, ohne diese zu beschädigen.




Nun folgen die beiden anderen Widerstände `R1` und `R2` (beige). Sie werden links und rechts vom Schriftzug angebracht. Die Reihenfolge ist dabei egal, du kannst auch gleich beide zusammen einbauen. Die Arbeitsschritte sind die gleichen wie beim ersten Widerstand.




*Gratulation.* Du hast den ersten Schritt gemeistert. Vergleiche dein Ergebnis mit dem Bild aus dieser Anleitung.

=== Kondensator
Als Nächstes ist der Kondensator an der Reihe. Suche nach dem kleinen orange-farbenen Bauteil in Form einer Linse. Die Position auf der Platine ist diesmal weiter zum anderen Ende bei der Markierung `C1`. Schaue auf das abgebildete Symbol.




So wie eben bei den Widerständen wird der Kondensator von oben in die Platine gesteckt und von der Rückseite festgelötet.




Nach dem Löten kannst du hier ebenfalls die überstehenden Draht-Enden abzwicken.




*Geschafft*. Dies war das Ende deiner Aufwärmrunde. Denn jetzt wird es eine Idee kniffeliger.

=== Schaltkreis-Sockel
Der Schaltkreis-Sockel hat ganze 14 Kontakte und das heißt für Dich, dass du Deine Lötfertigkeiten jetzt richtig trainieren kannst. Denn alle 14 Lötstellen sind identisch.




Die Position des Sockels auf der Platine kannst du nicht übersehen. Der Sockel hat auf einer Schmalseite eine kleine Kerbe und diese sollte, wie auf der Platine gekennzeichnet, nach vorne zeigen.




Achte beim Löten darauf, dass du zunächst erst eine Ecke und dann die schräg gegenüberliegende Ecke anlötest, falls du den Sockel noch ein wenig tarieren möchtest.




*Tada*. Du hast nun bereits 22 Lötstellen auf der Bakiwi-Platine gesetzt. Wenn du bisher nicht so viel gelötet hattest, solltest du spätestens jetzt den Dreh gut raushaben.

=== Taster
Der Taster wird an der Stelle mit der Markierung `PAUSE` eingesetzt. Wenn du den Taster spielend leicht einsetzen kannst _ohne_ die Beinchen zu biegen ist er auch automatisch richtig herum. Mitunter hörst du ein leises Knackgeräusch, wenn der Taster einrastet.




[IMPORTANT]
====
Die Lötstifte des Tasters sind ein wenig spitz, achte beim Einsetzen des Tasters auf deine Finger. Nach dem Einlöten solltest du diese Spitzen mit der Zange entfernen.
====



=== Spannungswandler
Das nächste Bauteil wird etwas schwieriger. Halte zunächst nach dem abgebildeten Symbol `VREG` auf der Platine Ausschau, es ist knapp über dem orangenen Kondensator zu finden und sieht aus wie ein angeschnittener Kreis.




*Achtung!* Jetzt wird es etwas fummelig. Der _Spannungswandler_ hat drei dünne Beinchen, die superdicht aneinander liegen. Damit du den Spannungswandler einsetzen kannst, muss das mittlere Bein etwas in Richtung der Rundung umgebogen werden, sodass die Enden der Drähte ein kleines Dreieck aufspannen. Du kannst eine Pinzette oder einen Bleistift zur Hilfe nehmen oder es vorsichtig mit deinem Fingernagel probieren.



Die richtige Anordnung der Beinchen ist bei diesem Bauteil entscheidend für seine korrekte Funktion. Achte daher darauf, dass die Form des Bauteils mit der auf der Platine abgebildeten Zeichnung übereinstimmt. Setze den Spannungswandler ein und drücke ihn wie abgebildet Stück für Stück weiter hinein. Dabei wird sich das mittlere Beinchen noch weiter verbiegen -- das ist in Ordnung.




Wenn der Spannungswandler bis auf die Platine gedrückt ist, sollte er kaum 1 mm höher sein als der Schaltkreissockel. Nun löte die drei Beine wie gehabt fest und kürze die Drähte nach dem Löten mit der Zange. Du wirst feststellen, dass die Lötstellen diesmal sehr dicht beieinander sind. Konzentriere dich gut, damit kein Kurzschluss entsteht.




*Gut gemacht*. Jetzt wird das Löten erst einmal wieder etwas einfacher, versprochen.

=== Batteriekabel-Buchsen




Setze nun die zwei weißen Batteriebuchsen bei den Markierungen `BAT1` und `BAT2` ein. Achte dabei darauf, dass du sie _genau_ wie auf der Platine abgebildet einsetzt. Die kleinen Lücken und Kerben an den Buchsen sind auch auf der Platine abgebildet. Die korrekte Ausrichtung ist hier sehr wichtig!




Mit ein wenig Geschick kannst du beide Buchsen im gleichen Arbeitsgang einsetzen und festlöten. Auch hier bietet es sich an, zunächst ein Beinchen festzulöten und noch mal die Ausrichtung zu korrigieren falls nötig.

[CAUTION]
====
Achtung! Vergleiche an dieser Stelle bitte noch einmal genau deine Platine mit den abgebildeten Fotos. Eine verkehrt herum eingelötete Batteriebuchse führt bei Anschluss der Batterie später zu einem Verpolen und endet möglicherweise in der Zerstörung von Teilen deines Bakiwi. Daher schau lieber zweimal hin.
====

=== An/Aus-Schalter

Weiter geht es mit dem Einsetzen des An/Aus-Schalters. Dieser ist blau/weiß und wird auf der Platine bei der Markierung `POWER` platziert. Wichtig ist hierbei, dass das weiße Teil Richtung `off` zeigt. Prinzipiell kannst du den Schalter auch andersherum einlöten, er funktioniert in beide Richtungen gleichermaßen. Stelle bloß sicher, dass er in der `OFF`-Position ist, d. h. dass dein Bakiwi ausgeschaltet ist, wenn wir später die Batterien einlegen.




[CAUTION]
====
Zuviel Hitze lässt den Schalter schmelzen und kann ihn unbrauchbar machen, daher achte beim Löten darauf, Stift und Lötfläche stets gleichzeitig aufzuheizen, damit der Lötvorgang kurz und effektiv ist.
====




Die Lötstifte sind recht lang und sollten nach dem Festlöten ein wenig gekürzt werden. Das Material der Schalterstifte ist auch dicker als das der anderen Bauteile, sodass du etwas mehr Kraft beim Abknipsen benötigst.

=== Stiftleisten

Widme dich nun den drei Stiftleisten. Die beiden einreihigen Stiftleisten (1x3) werden mit dem kurzen Ende von oben in die Platine bei `MOT1` und `MOT2` eingesteckt und wie gehabt auf der Rückseite festgelöten. An ihnen werden später die Motoren deines Bakiwi angeschlossen.




Am besten setzt du beide Stiftleisten zusammen ein, drehst dann die Platine und stellst sie wie in der Abbildung gezeigt auf die noch etwas wackeligen Stiftleisten. Achte darauf, dass die Stifte möglichst senkrecht zur Platine stehen. Wenn du zuerst an jeder Stiftleiste nur einen Stift festlötest, kannst du die genaue Position durch nochmaliges Aufheizen korrigieren, sollte sie nicht gleich beim ersten Mal gerade sein.




Die doppelreihige Stiftleiste (2x3) wird bei `PROG` ebenfalls mit Ihrem kurzen Ende von oben eingesetzt. Das Einlöten sollte nun einfacher sein, weil die beiden verlöteten einreihigen Stiftleisten bereits die Platine stabilisieren. Die doppelreihige Stiftleiste ist der Programmieranschluss, falls du später das Programm deines Bakiwi verändern möchtest.

=== Leuchtdioden

Dein Bakiwi bekommt zwei Leuchtdioden (LED) um dir den Zustand des Lauf-Oszillators anzuzeigen. Die Position der LEDs ist mit `D1` und `D2` markiert. Farblich kannst du selbst entscheiden, welche LED auf welche Seite soll. Du kannst auch andersfarbige LEDs einbauen, wenn du welche hast.




[IMPORTANT]
====
Leuchtdioden haben eine sogenannte _Polarität_, d. h. es ist _nicht_ egal, wie herum sie eingebaut werden. Erkennen kannst du das anhand der unterschiedlich langen Beine. Das längere Bein ist immer der Pluspol, das kürzere Bein ist der Minuspol. Du kannst dir das gut merken, wenn du dir vorstellst, dass du gedanklich ein _Pluszeichen_ auseinander baust und die Striche hintereinanderlegst (`+` -> `--`). Dann ist das _Plus_ länger als das _Minus_. Diese Merkregel gilt übrigens für alle zweibeinigen elektronischen Bauteile mit Polarität und unterschiedlich langen Beinen.
====




Setze also die Leuchtdioden gemäß ihrer Polarität und deiner Wunschfarbe ein und löte sie fest. Die Beine kannst du danach wie immer kürzen.

=== Elektrolytkondensator

Der Elektrolytkondensator (kurz: _Elko_) wird genau wie im vorherigen Schritt (langes Bein = Pluspol) eingebaut. Seine Position ist mit `C2` markiert. Der Minuspol ist sogar auf dem zylinderförmigen Gehäuse mit einem dicken (hohlen) Minus gekennzeichnet.




[NOTE]
====
Die Farbe deines Bakiwi-Elkos kann von der in der Abbildung abweichen, das hat aber keinen Einfluss auf die Funktion. Je nach Hersteller haben auch die Elkos einen Papierstreifen, der die Beinchen stabilisiert. Entferne ihn vorsichtig vor dem Anlöten.
====



=== Potentiometer

Dein Bakiwi bekommt vier Drehknöpfe, mit denen du seine Gangart verändern kannst. Diese Bauteile heißen Potentiometer und sind verstellbare Widerstände. Du kennst das vom Lautstärkeknopf bei Lautsprechern oder anderen Geräten.




Lege dir die vier blauen Potentiometer (kurz: _Potis_) mit den zugehörigen Drehknöpfen vor dich hin. Stecke die Drehknöpfe mit dem Pfeil nach oben in die Potis ein (siehe Abbildung).



Danach kannst du die zusammengesteckten Teile auf die Positionen `LEVEL`, `SPEED`, `PHASE` und `BALANCE` verteilen und vorsichtig die Platine wenden. Die Potis sitzen in der Regel schon recht fest und fallen nicht so leicht von allein ab.




Jetzt kannst du alle vier Potis nach und nach festlöten. Nach dem Löten solltest du auch hier die spitzen Enden etwas kürzen.

:numbered!:

=== Pause

Du hast jetzt schon eine ganze Menge Bauteile eingelötet. Falls du bis hierhin durchgearbeitet hast, empfehlen wir dir, eine kurze Pause einzulegen. Sorge für dich, indem du etwas frische Luft schnappst, etwas trinkst oder isst, und vor allem deine Augen entspannst. Das Arbeiten im Nahfeld kann für deine Augen anstrengend sein und etwas Entspannung zwischendurch kann nicht schaden.

image:./make_a_break.jpg/[width=100%]

:numbered:

=== Batteriefächer

Nun kannst du die Platine kurz beiseitelegen und dir die beiden Batteriefächer schnappen. Zu jedem Fach gibt es ein rot-schwarzes Kabel mit weißem Stecker.

[WARNING]
====
Auch wenn es verlockend ist: Bitte jetzt noch keine Batterien einlegen!
====

Die Kabel müssen an den Lötlaschen der Fächer festgelötet werden, dazu kannst du die abisolierten Kabelenden in die Löcher einstecken. Es ist einfacher, wenn du die Laschen dazu ganz leicht hochbiegst.
Achte darauf, dass die Kabel von der flachen Seite des Fachs wegzeigen. Das ist später die Innenseite wo die Motoren sitzen und du musst vermeiden, dass die Batteriekabel in die Beine deines Bakiwi gelangen.

Die korrekte Polarität der Kabel ist hier von größter Wichtigkeit. Hier gilt dasselbe wie für die Batteriebuchsen, bei Verwechslung von Plus und Minus können Teile deines Bakiwi kaputt gehen. Das rote Kabel steht für _Plus_ das schwarze Kabel für _Minus_. Diese Konvention ist weit verbreitet und es lohnt, sich das zu merken. Die Polarität der Batteriefächer kannst du auf deren Innenseite ablesen.






Die einlegten Kabel nun am äußersten Ende der Lasche festlöten. Dabei so effizient und schnell wie möglich löten, damit das Plastik der Batteriefächer nicht schmilzt.
[CAUTION]
====
Das Plastik der Batteriefächer ist recht temperaturempfindlich. Eine Berührung mit dem Lötkolben oder ein zu langes Aufheizen der Lötlaschen lässt das Batteriefach schmelzen und kann es schlimmstenfalls unbrauchbar machen.
====




=== Mikrocontroller

Bei dem folgenden Arbeitsschritt wird ausnahmsweise mal nicht gelötet. Du kannst jetzt den _Mikrocontroller_, einen sogenannten _Integrierten Schaltkreis_ (kurz: Chip) in den Sockel einsetzen. Dazu musst du den Schaltkreis mit seinen 14 Beinchen zunächst etwas vorbereiten. Halte den Chip wie in der Abbildung gezeigt und biege jeweils alle sieben Beine einer Seite ganz vorsichtig etwas weiter nach innen. Nutze dazu z. B. die Tischplatte. Wiederhole den Schritt mit den anderen sieben Beinchen.

Anfangs zeigen die Beine etwas nach außen. Im Idealfall zeigen sie nach dem Biegen genau senkrecht vom Chip-Körper in dieselbe Richtung. So lässt sich der Chip leichter in den Sockel einsetzen.




Setze nun den Mikrocontroller in den Sockel, achte darauf, dass alle Beinchen in ihrer Führung sitzen. Wichtig hierbei ist, dass die Kerbe am Chip mit der Kerbe am Sockel in die gleiche Richtung (zum Taster nach vorn) zeigen.




=== Fühler

Der letzte Lötarbeitsschritt, um deine Bakiwi-Platine zu vervollständigen, ist die Anbringung der Fühler. Deinem Bausatz liegen zwei kurze Stücke Gitarrensaite bei. Diese kannst du als Grundlage für die Fühler deines persönlichen Bakiwis verwenden -- musst du aber nicht. Du kannst viele verschiedene metallische Materialien verwenden:

* Kabel mit farbiger Isolierung
* Messingdraht
* Pfeifenputzer
* oder etwas ganz anderes




Die benutzten Fühler werden von Bakiwi automatisch eingelernt. Es kann sein, dass sie anfänglich noch nicht sensibel genug oder gar übersensibel sind. Aber nach ein paar Minuten kann dein Bakiwi seine von dir individuell gestalteten Fühler genau richtig benutzen. Fühle dich also frei in der Gestaltung, alles ist erlaubt solange es:

* an die entsprechenden Flächen angelötet werden kann
* ein leitfähiges Material ist
* und keine leitenden Teile der Platine berührt

*Probier verschiedenes aus!*

Wenn du keine anderen Materialien verfügbar hast, kannst du auch die beiliegenden Gitarrensaiten frei umgestalten. Mit Puscheln oder flauschigen Enden, oder du kannst Ösen anlöten und etwas drumbinden. Die Saiten sind gut lötbar, biegsam, leitfähig und sind recht robust und knicken nicht so leicht. Hier zwei Beispiele:




Zum Anlöten lege die Platine mit den Bauteilen nach oben auf den Tisch und löte die Fühler als erstes einmal _oben_ an der Platine fest und danach auf der Rückseite wie gewohnt. So hast du bessere Kontrolle über deren Ausrichtung.

[NOTE]
====
Bedenke, es gibt an dieser Stelle für deinen Lötkolben möglicherweise mehr Metall als üblich aufzuheizen, sodass du hier gegebenenfalls ein paar Sekunden länger die Lötspitze dranhalten musst. Die großen Lötflächen und der dicke Draht nehmen viel Wärme auf und werden heiß, achte auf deine Finger!
====




== Nach dem Löten

=== Aufräumen

*Trommelwirbel.... Ka--tsching.* Geschafft. Die Lötarbeiten sind nun abgeschlossen. Die Lötstation wird jetzt nicht mehr benötigt und du kannst sie abschalten und abkühlen lassen.

[WARNING]
====
Die Lötspitze kann nach dem Abschalten noch ein paar Minuten sehr heiß sein. Lass also die Lötstation noch eine Weile abkühlen, bevor du sie wegräumst.
====

Zum Abschluss empfehlen wir, die Lötstellen auf der Rückseite noch einmal anzugleichen und zu lange Stiftereste zu kürzen. Das ist wichtig, damit nachher beim mechanischen Zusammenbau keine störenden Spitzen mehr da sind, die sich in die Motor- bzw. Batteriekabel bohren könnten.




//TODO Abschnitt überarbeiten

=== Abfallentsorgung

Wir haben versucht, den Bausatz so zu gestalten, dass möglichst wenig Müll anfällt. Bitte trenne den Müll. Alle kleinen Metallreste können zum Verpackungsmüll (Gelbe Tonne) und die Papierfetzen zum Altpapier. Die beiliegenden Zipper-Tüten und den Karton kannst du vielleicht ja noch weiter nutzen oder entsorgst sie ebenfalls zum Verpackungsmüll bzw. Altpapier.

=== Funktionstest
Bevor es gleich mit dem mechanischen Zusammenbau losgehen kann sollten die elektronischen Komponenten getestet werden. Wenn du also ein Multimeter zur Hand hast, kannst du dein Board auf Kurzschlüsse testen.

==== Kurzschlusstest




Nimm ein Multimeter zur Hand und schalte es in den Modus Durchgangsprüfung ("Piepser"). Du erkennst das an dem Lautsprecher-Symbol. Halte die beiden Prüfspitzen mit den metallischen Enden gegeneinander und überzeuge dich, dass es einen deutlich hörbaren Piepton gibt. Das akustische Signal zeigt dir einen elektrischen Kontakt ohne nennenswerten Widerstand dazwischen an. Du kannst es dazu nutzen Lötstellen, Kabel und Stecker auf ordnungsgemäßen Kontakt zu prüfen oder auch um ungewollte Kurzschlüsse zu finden.




Halte nun die Prüfspitzen an die beiden Stifte der linken Batteriebuchse, hierbei sollte kein Signal ertönen. Wiederhole den Test mit der anderen Buchse. Teste ebenfalls die Stifte der beiden Motoranschlüsse und des 6-poligen Programmieranschlusses, indem du jeweils zwei benachbarte Stifte auf Kurzschluss prüfst. Sollte es hier bei zwei Stiften piepsen, d. h. einen Kontakt geben, musst du dir deine Lötstellen an dieser Stelle noch einmal sehr genau anschauen. Möglicherweise ist etwas Lötzinn zwischen die Lötstellen geraten und verbindet diese. Achte auf genügend Licht bei der Kontrolle und nimm ggf. eine Lupe zur Hilfe.

[TIP]
====
Sollten zwei Lötstellen aus Versehen mit Lötzinn miteinander verbunden sein, kannst du durch erneutes Aufheizen der Lötstellen versuchen diese voneinander zu trennen. Wenn das Lot dabei klebrig wirkt, so versuche etwas frisches Lötzinn (mit noch nicht verdampften Flussmittel) hinzuzufügen um die Lötstellen wieder gängig zu machen. Der farbige Lack (blau oder lila) auf deiner Platine nimmt Lötzinn nicht an und hilft dir die Lötstellen zu trennen. Wenn beide Lötstellen gemeinsam aufgeheizt werden und durch genügend Flussmittel gut fließen können trennen sie sich leicht voneinander und ziehen sich auf ihre Lötflächen zurück.

Eine optische Inspektion kann bereits viele mögliche Fehlerquellen ausschließen. Eine gute Lötstelle sieht immer ein wenig aus wie ein kleiner Vulkan oder Berg. Wenn die Lötstelle eher wie eine Kugel aussieht kann das ein Anzeichen dafür sein, dass zu wenig Lötzinn auf der Lötfläche gelandet ist.
In diesem Fall ist der Kontakt möglicherweise nicht zuverlässig.
====



Teste als Letztes den Pluspol der linken Batteriebuchse gegen den Minuspol der rechten Batteriebuchse. Es sollte hier ebenfalls kein Kontakt zu messen sein. Stelle nun den An-/Aus-Schalter auf `ON` und messe nocheinmal. Nun sollte es Kontakt geben und piepsen. Stelle danach den Schalter wieder auf `OFF`.



==== Motoren verbinden
[#connect_motors]

Verbinde nun die Motoren. Achte darauf, dass die braunen (bzw. schwarzen) Adern des 3-adrigen Motorkabels mit dem Stift verbunden ist, der auf der Platine mit dem Ground-Symbol (siehe Abbildung) bezeichnet ist.




Lege nun die Batterien ein. Hierbei ist es sehr wichtig, die im Innern des Batteriefachs angezeigte Polarität (+/-) zu beachten. Auf deinen Batterien oder Akkus sind ebenfalls die Symbole Plus und Minus zu erkennen (manchmal nur das Plus). Verbinde nun die Batteriestecker mit den Buchsen auf der Platine, dabei ist es egal, welches Fach du an welchen Stecker anschließt.




[WARNING]
====
*Aufgepasst!* Sollten nach dem Anschließen der Fächer die Batterien warm oder gar heiß werden, musst du die Stecker sofort wieder von der Platine trennen. Das Aufheizen der Batterien deutet sehr wahrscheinlich auf einen Kurzschluss hin und du musst noch einmal die elektrische Durchgangsprüfung wiederholen und deine Lötstellen genau inspizieren, um den Kurzschluss zu finden.
====

Stelle nun den An-/Aus-Schalter auf `ON` und wenn alles richtig zusammengebaut ist, solltest du nun bereits die Leuchtdioden blinken sehen. Wenn alle Drehknöpfe mit den Pfeilen nach oben zeigen, sollten die Leuchtdioden im Gleichtakt blinken.

Wenn die Leuchtdioden funktionieren, dann betätige nun den Taster und gleich darauf sollten beide Motoren beginnen Geräusche zumachen und die Schäfte zu drehen (die Runden gezahnten Metallenden).

Berühre die Fühler mit deinen Händen und sofort sollten die Geräusche der Motoren sich verändern, langsamer werden oder gar stoppen. Beim Loslassen der Fühler sollten die Motoren wieder ihr ursprüngliches Verhalten aufnehmen. Schalte den Bakiwi nun wieder aus.

Wenn bis hierhin alles wie erwartet funktioniert, kannst du jetzt zum nächsten Kapitel übergehen, dem <<assembly, mechanischen Zusammenbau>>.

Sollte ein Motor sich drehen, der andere aber nicht, stelle sicher, dass alle Drehknöpfe nach oben zeigen und dass die Motorkabel angeschlossen sind wie in Abschnitt <<connect_motors, Motoren verbinden>> beschrieben steht.

=== Was tun, wenn etwas kaputt gegangen ist?

Wenn dir während des Lötens oder beim Zusammenbau ein Bauteil kaputt oder verloren gegangen sein sollte: Keine Panik! Wir senden dir gerne ein neues zu. Schicke uns dazu einen Brief mit dem kaputten Teil und dazu einen an dich adressierten Rücksende-Umschlag und wir sorgen sofort für Ersatz. Wir freuen uns, wenn du dir die Zeit nimmst und uns kurz beschreibst wie das Bauteil kaputt gegangen ist, sodass wir unseren Bakiwi-Bausatz mit deiner Hilfe verbessern können.

Wenn ein Problem besteht, du aber nicht ganz sicher bist, was die Ursache ist, kannst du uns auch Fotos von der Platine senden (z. B. von Ober- und Unterseite) und wir werden versuchen zu helfen, die Fehlerquelle zu identifizieren.

== Mechanischer Zusammenbau
[#assembly]

:imagesdir: ./img/02_mechanics/

=== Vorbereitung

Hole die abgebildeten mechanischen Bauteile aus der Packung und lege sie vor dir ab. Die Bakiwi-Platine und die Batteriefächer hast du bereits in vorausgehenden Arbeitsschritten vorbereitet.



Für den Zusammenbau benötigst du weitere Werkzeuge: einen kleinen Kreuz-Schraubendreher und einen Innensechskant-Schraubendreher (2,5 mm). Wenn vorhanden, ist eine Pinzette evtl. nützlich und vereinfacht den Zusammenbau, ist aber nicht zwingend erforderlich. Weiterhin wird noch einmal der Seitenschneider benötigt.



=== Motoren einbauen

Wir beginnen den Zusammenbau mit den Motoren. Nimm dir dazu einen der Motoren und einen Motorhalter sowie zwei der vier Kreuzschrauben (du erkennst sie daran, dass es die einzigen sind die Spitzen haben). Lege das Motorkabel wie abgebildet einige Male in Falten und drücke es sachte zusammen, sodass es sich beim Einbauen leichter in dieselben Falten legt.




Fädele das Motorkabel durch die große Öffnung in den Halter und durch die kleine seitliche Öffnung wieder aus dem Halter heraus. Setze nun den Motor in den Halter, wobei es wichtig ist, dass sich ein Teil des Kabels gefaltet im Halter befindet, damit insgesamt weniger vom Kabel heraussteht. Der Schaft des Motors sollte von der kleinen Öffnung wegzeigen (vergleiche dein Ergebnis mit der Abbildung).




Setze nun nacheinander die Schrauben an und ziehe sie hinreichend fest. Wenn alles gut sitzt, wiederhole die Schritte mit dem zweiten Motor.




=== Rahmen zusammensetzen

Als Nächstes füge den Rahmen zusammen. Lege dazu die Grundplatte des Rahmens vor dir ab und setze die v-förmige Klemmenmutter zwischen die beiden mittigen Lochstege. Setze die Arretierschraube ein und ziehe sie zwei Umdrehungen an.




Lege die beiden Motorhalter mit ihren Achsenden auf die Löcher in der Grundplatte. Achte darauf, dass die Öffnungen und die herausragenden Kabel nach oben wegzeigen. Lege nun den Deckel des Rahmens auf und halte alles mit deinen Fingern zusammen. Wenn du die Arretierschraube sachte noch etwas weiter hinein drehst, hält der Rahmen besser zusammen.




==== Kabel einfädeln und verstauen

Halte den Rahmen so, dass ein Motor nach links der andere nach rechts zeigt und die Kabel nach oben herausragen. Fädele nun das von dir aus linksseitige Motorkabel durch das von dir wegzeigende hintere Loch. Das rechtsseitige Motorkabel gehört durch das zu dir hinzeigende Loch.

Verstaue die beiden Motorkabel im Rahmen über der Klemmenmutter, sodass in etwa noch 4 cm Kabel aus dem Rahmen ragen.




==== Platine festschrauben
Nun benötigst du die zwei Zylinderkopfschrauben (M3x10mm) und den Innensechskant-Schraubendreher. Setze nacheinander die Schrauben oben in die Löcher der Bakiwi-Platine ein und schraube diese am Rahmen fest.

[TIP]
====
Mit etwas Glück lassen sich die Schrauben auf den Innensechskant-Schraubendreher aufstecken und halten dort gut durch Reibung fest, manche Werkzeuge sind auch magnetisch. Damit lassen sich die Schrauben meist leichter in die Löcher der Platine einsetzen.
====

[NOTE]
====
Achtung, beim ersten Einschrauben schneiden sich die Schrauben ihr eigenes Gewinde in die Löcher der Rahmengrundplatte. Solltest du die Schrauben später noch einmal lösen und wieder einsetzen wollen, versuche das Gewinde zu ertasten, indem du die Schraube vor dem festziehen leicht linksherum drehst, bis sie ins ursprüngliche Gewinde findet.
====



Der Rahmen hält nun von selbst zusammen, ziehe die Arretierschraube vorsichtig mit den Fingern etwas fester und teste wie sich die Motorhalter nun in bestimmten Rastpositionen feststellen lassen.

=== Motorkabel verbinden

Nun werden die Motoren verkabelt. Diesen Schritt hatten wir bereits beim Testen, stelle erneut sicher, dass die braunen (bzw. schwarzen) Adern der Motorkabel auf das Ground-Symbol zeigen (vgl. mit Abschnitt <<connect_motors, Motoren verbinden>>). Verstaue die beiden Motorkabel möglichst weit im Rahmen, sodass sie gut anliegen und keine großen Schlaufen bilden.




=== Batteriehalter anbringen

==== Vorbereiten

Bereite nun das Anbringen der Batteriehalter vor. Du benötigst die vier M3x4mm Zylinderkopfschrauben, den Innensechskant-Schraubendreher und den Seitenschneider.



Entferne zunächst die beiden Distanzstege in beiden Batteriefächern, indem du sie ganz knapp über der Fläche abtrennst. Schraube nun die Batteriefächer seitlich an den Rahmen an. Jetzt ist genügend Platz für die Schraubenköpfe.




==== Festschrauben

Die Batteriefächer sollten so angebracht werden, dass die Kabel an der Seite mit den Fühlern sind. Jeder Halter wird mit zwei Schrauben am Rahmen fixiert. Auch hier Schneiden sich die Schrauben beim ersten Mal einsetzen ihr Gewinde in die Löcher im Rahmen.

[CAUTION]
====
Warnung! Nach fest kommt locker! Achte darauf, die Schrauben nicht zu fest anzuziehen.
====



==== Batteriekabel verlegen

Verlege die Batteriekabel hinter den Motorkabeln entlang der Platine bis nach hinten und stecke sie dort in die Buchsen ein. Schiebe das Kabel ggf. vorsichtig etwas unter die Platine.




*Hurra!* Der Körper deines Bakiwi ist nun fertig. Vergleiche noch mal mit der Abbildung die Ausrichtung der Stecker auf deiner Platine und ob alle Kabel möglichst dicht am Bakiwi-Körper anliegen.



=== Beine anbringen

Lege zunächst die Batterien wieder ein und schalte dein Bakiwi ein. Drücke zweimal nacheinander im Abstand von ca. einer Sekunde den `PAUSE`-Knopf, sodass dein Bakiwi seine Motoren in die Ausgangsposition fährt und dann wieder in den Pausemodus geht.




Nun setze die abgebildeten Bein-Anschlüsse auf die gezahnten Enden der Motorschäfte und schraube sie mit den beiliegenden Kreuzschrauben fest. Es sind die letzten zwei Schrauben, die übrig sind.

Die beiliegenden 3D-gedruckten Bein-Anschlüsse sind nur eine von unzähligen Möglichkeiten wie du deinem Bakiwi Beine geben kannst. In deinem Bausatz liegen mitunter noch weitere Teile, die auf die Schäfte der Motoren passen (sogenannte Ruderhörner).

*Probiere dich aus!* Mit den beiliegenden restlichen Ruderhönern kannst du verschiedene Beinpaare aus unterschiedlichen Bastelmaterialien herstellen immer wieder wechseln.




*Erledigt!* Je nachdem welchen Bakiwi-Bausatz du hast, liegen unter Umständen noch kleine Lego-Teile bei, welche die ersten Füße deines Bakiwi sein können. Vielleicht besitzt du auch bereits Lego-Technic-Teile. Diese kannst du verwenden, um sehr schnell Beine und Füße für dein Bakiwi zu entwerfen.



== Wie Du Dein Bakiwi spielst und wie es funktioniert

=== Vor dem Einschalten

*Wichtig:* Vor dem ersten Einschalten (mit Beinen dran) schau dir die Bezeichnungen der vier grauen Regler (Potentiometer) genauer an.

. Stelle den `BALANCE` und `PHASE`-Regler auf Mittelposition (Pfeil nach oben).

. Stelle den Geschwindigkeitsregler (`SPEED`) auf halb links (in Richtung der langen Welle).

. Stelle den `LEVEL`-Regler auf halb links (in Richtung der kleinen Welle).

Schalte nun dein Bakiwi ein.

=== Die Funktionsweise erklärt

:imagesdir: ./img/04_usage/

OSC

Im Programmspeicher deines Bakiwi-Mikrocontrollers sind zwei Neuronen, welche so verschaltet sind, dass sie schwingen. Sie bilden zusammen einen sogenannten Oszillator und dieser ist der Taktgeber für die Bewegung der Beine.
Die beiden Leuchtdioden deines Bakiwi signalisieren die Aktivität dieser Motorneuronen. Im Pause-Modus sind die Neuronen und somit der Oszillator bereits aktiv und schwingen, die Motoren sind aber inhibiert (gehemmt). Das heißt, du kannst durch das Verstellen der vier Regler das Bewegungsmuster jederzeit verändern, ob pausiert oder nicht.

Wir haben ein Video aufgezeichnet, um die Funktionsweise besser zu illustrieren:

ifdef::env-github[]
link:https://youtu.be/rAteGra5-xM[Direkter Link aufs Video^]


endif::[]

ifndef::env-github[]
video::rAteGra5-xM[youtube, width=640, height=360]
endif::[]

=== Laufparameter

Die Art, wie dein Bakiwi läuft, wird durch mehrere Faktoren beeinflusst. Maßgeblich für eine erfolgreiche Fortbewegung sind die Beine, die du deinem Bakiwi erschaffst. Hast du dir neue Beine für dein Bakiwi ausgedacht, so kannst du mit der Veränderung der folgenden Parameter (Stellschrauben) deinem Bakiwi mit seinen neuen Beinen das Laufen beibringen:

==== Anstellwinkel

Die Anstellwinkel sind rein mechanische Parameter. Du kannst durch Lösen der großen Arretierschraube die Motorhalter beweglich machen und dann ihre Winkel zum Körper und zueinander verändern. *Probiere Verschiedenes aus!* Ziehe die Schraube dann wieder nur soweit fest, bis die Motorhalter in der gewünschten Position fest genug halten.

==== Geschwindigkeit/Frequenz

SPEED

Bewege den `SPEED`-Knopf und beobachte, wie sich die Geschwindigkeit des Blinkens der LEDs verändert. Verlasse den Pause-Modus durch Drücken des Tasters und beobachte an den Motoren wie sich die Geschwindigkeit der Schwingung (d. h. die Frequenz der Oszillation) der Motorneurone unmittelbar auf die Motoren auswirkt. Die Frequenz regelt die Schrittgeschwindigkeit deines Bakiwi.

[TIP]
====
Wir empfehlen zunächst mit einer langsamen Bewegung zu beginnen. Es hilft dir dabei die Bewegung deiner selbst-gebauten Beine gut beobachten zu können und damit ein gutes Verständnis über die Auswirkungen der Beinbewegung zu bekommen.
====

==== Level/Amplitude

LEVEL

Drehe am `LEVEL`-Knopf und beobachte, wie sich die Helligkeit der LEDs verändert und die Weite mit der die Motoren bei jeder Bewegung ausschlagen. Diese Schwingungsweite wird Amplitude genannt und regelt die Schrittweite der Laufbewegung.

==== Balance

BALANCE

Drehe am `BALANCE`-Regler und beobachte wie sich die vorher eingestellte Amplitude auf die beiden Motoren verteilt. Steht der Regler in der Mittelposition, sind beide Motoramplituden gleich. Ein Drehen nach links, senkt die Amplitude des vorderen Motors, eine Drehung nach rechts dämpft die Bewegung des hinteren Motors.

==== Phase

PHASE

Der letzte Parameter, die sogenannte Phase (bzw. der Phasenwinkel) ist wahrlich die besondere Würze und regelt die Laufrichtung. Ein `PHASE`-Regler auf Mitte erzeugt eine synchrone aber gegenläufige Bewegung der Motoren. Drehst du den Phasenwinkel etwas aus der Mitte heraus, bewegen sich die Motoren nicht mehr synchron, was entscheidend für das Laufen ist. Ein bis auf Maximum (oder Minimum) gestellter Phasenwinkel erzeugt erneut eine synchrone aber diesmal mitläufige Bewegung. Die Phase ist der wichtigste Parameter für eine erfolgreiche Laufbewegung und benötigt deine besondere Aufmerksamkeit. Mit Ihr entscheidet sich, ob sich dein Bakiwi überhaupt von der Stelle bewegt und wenn ja in welche Richtung.

Jetzt aber genug gelesen...

*Ran ans Werk!* :)

=== Zentrierung

Wenn du dein Bakiwi zusammengebaut hast, solltest Du seine Beine ggf. zunächst zentrieren. Die Motoren mit den aufgesteckten Bein-Anschlüssen sind herstellungsbedingt nie perfekt gerade. Diesen Versatz kann dein Bakiwi korrigieren und es sich merken.

Schalte dazu dein Bakiwi zunächst aus.

. Halte den Pause-Taster gedrückt und schalte dein Bakiwi bei gehaltenem Taster wieder ein. Die LEDs sollten jetzt schnell flackern.

. Lasse den Taster los und nun sollte nur noch die linke LED flackern und der vordere Motor kurz anfahren. Wenn du nun den `PHASE`-Drehknopf betätigst, kannst du den vorderen Motor in die gewünschte Ausgangsposition stellen. Justiere dabei solange, bis der Beinanschluss gerade ist.

. Betätige den Taster erneut um zum Bestätigen. Nun flackert die rechte LED und du kannst den Prozess für den hinteren Motor durchführen.

. Ist auch der hintere Motor richtig gerade eingestellt, bestätige erneut durch Drücken des Tasters und der Zentrierungsprozess ist damit abgeschlossen.

[TIP]
====
Wenn du deinem Bakiwi neue Beine baust und dabei die Beine, ob gewollt oder ungewollt, nicht gleich werden kannst du die Zentrierung ebenfalls benutzen, um Unsymmertrie auszugleichen.

Du kannst es aber auch gezielt verwenden, um dein Bakiwi immer eine Kurve laufen zu lassen.
====

=== Der Schaltplan

Im Folgenden siehst du den elektrischen Schaltplan deines Bakiwi. Findest du selbst heraus, welche Symbole zu welchen von dir gelöteten Teilen gehören? Einen Schaltplan zu _lesen_ erfordert etwas Übung, aber nachdem du jetzt alle Teile selbst zusammengelötet hast, kannst du hier nachvollziehen, welches Bauteil mit welchem verkabelt ist. Die _Kabel_ auf einer Platine heißen Leiterbahnen und bestehen aus einer dünnen Lage Kupfer. Wenn du die Platine deines Bakiwi anschaust und leicht gegen das Licht hältst, kannst du sie unter der Lackschicht ausmachen. Manche Leiterbahnen wechseln die Seite der Platine durch kleine Löcher, sogenannte _Vias_. Manche Leiterbahnen sind auch ganze Flächen, und so ist beispielsweise die gesamte untere Kupferfläche der Platine der Minuspol.

Ein Schaltplan hilft auch bei der Fehlersuche. Verhält sich die Elektronik merkwürdig, sind ein Multimeter und ein Schaltplan die wichtigsten Hilfsmittel beim Finden der Ursache. Im Schaltplan sind auch die Bauteile genau bezeichnet. Du findest dort beispielsweise, Widerstandswert, welche Kapazität die Kondensatoren haben, in welche Richtung die Dioden geschaltet sind oder wie die Bezeichnung des Spannungswandlers ist. Mit der Hilfe eines Schaltplans kann ein elektrisches Gerät, wie auch dein Bakiwi, immer wieder repariert werden.

:imagesdir: ./img/


// === Die Bauteile und ihre Funktion
// TODO
// Kondensator, Widerstand, uC, Schalter, Taster, etc

// === Was ist ein Oszillator?
// TODO
// Amplitude, Phase, Frequenz
:numbered!:

== Hast du noch Fragen?
Du hast noch Fragen oder wünscht dir weitere Erklärungen? Du hast Anregungen oder Feedback für uns?
link:https://jetpack.cl/bakiwi[Schreib uns!]

Du kannst uns auch auf Twitter folgen, dann versorgen wir dich mit Neuigkeiten zu *#bakiwi*. Wir sind  link:https://twitter.com/labjetpack[@LabJetpack].

Ansonsten wünschen wir dir viel Spaß mit deinem neuen Bakiwi. Lass es krabbeln!

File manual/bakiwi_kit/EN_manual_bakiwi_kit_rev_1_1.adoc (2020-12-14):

=  Bakiwi Kit Assembly Manual
Doc Writer <kubisch@informatik.hu-berlin.de>
v0.21, 2020-12-15
:toc:
:toc-placement!:
:toc-title: Table of Adventures
:imagesdir: ./img/
:favicon: {imagesdir}icons/favicon.png
:stylesheet: bak.css
:linkattrs:

:numbered:
:numbered!:

ifdef::env-github[]
:tip-caption: :bulb:
:note-caption: :information_source:
:important-caption: :heavy_exclamation_mark:
:caution-caption: :fire:
:warning-caption: :warning:
endif::[]

_(Translation provided by Sebastian Schmölling and Mamun Azmy)_



toc::[]

:imagesdir: ./img/01_electronics/

== Preparation

=== Tools
You will need the following tools to solder the Bakiwi electronics:

* Soldering iron (or station) with a thin solder tip
* Tin solder (recommended: thickness 0.5-0.75mm with integrated flux, lead-free)
* Brass wool with container ("dry cleaner"), alternatively a moistened sponge
* Diagonal cutters or pliers
* Multimeter (optional)




[NOTE]
====
If you have no soldering experience at all, we recommend that you watch an introductory video or tutorial beforehand in order to get a rough idea of soldering. It is even better if you assemble the kit with someone else who can already do a little bit of soldering.
====

=== View components
Check all components for completeness. In addition to the parts shown, you may have included material that is suitable for the antennae of your Bakiwi, e. g. pieces of guitar strings or pipe cleaners.



Put all the small parts in a container so that none can be lost. First, take the Bakiwi board and place it in front of you so you can read the Bakiwi label. The _top_ of the board is the one with all the component labels. All components will now be inserted and soldered one by one in individually explained steps. Each component is inserted from the top and soldered on the _bottom_.




Turn on the soldering station and check the temperature display. If the temperature is adjustable, set it to match the recommended temperature of your solder (note the label). If you are unsure, start with 330°C, depending on the performance of the soldering station, a slightly higher temperature may be necessary. If the soldering feels sticky, then the temperature might be too low. If needed, gradually increase the temperature until the solder melts easily.

[TIP]
====
If your soldering tip no longer shines even with constant cleaning and keeps getting dark, the temperature is probably set too high.
====

=== Take your time!

Soldering your Bakiwi requires calm and concentration. The time required varies from person to person and depends very much on previous knowledge. Absolute newbies should plan 2 hours for soldering, professionals can do it in 30 minutes.

:numbered:
== Solder the components

=== Resistors

Look for the resistors. There is _one blue_ and _two beige_ ones. Start by peeling off the paper at either end of the blue resistor.




Now bend the two wire ends with your fingers directly at their origin so that they both point in the same direction and the two wires are parallel to each other. The blue resistor has the name `R3`. Look for the resistor symbol shown on the circuit board, it is located directly below the Bakiwi-label. Place it on the circuit board as shown in the picture. A resistor has no polarity, so it doesn't matter which way you put it in.




Hold the inserted component with your fingers, carefully flip over the circuit board and place it in front of you. Now start to solder the wire ends to the bottom side of the board. Make sure to touch and heat the wire and the soldering pad around the hole at the same time as you add the solder. The heat transfer works best when the soldering tip is clean and slightly coated with tin.




After that remove the wire ends by snapping them off with suitable pliers (e.g. wire cutters). Remove the wire as close as possible to your solder joint without damaging it.




Now take the other two resistors, `R1` and `R2` (beige). They are attached on either side of the Bakiwi-label. The order does not matter, you can also install both together. The steps are the same as for the first resistor.




*Congratulations.* You have taken the first step. Compare your result with the picture.

=== Capacitor

Now it’s the capacitor's turn. Look for the small orange lense shaped component. Take the circuit board and look for the `C1`-marking.




As with the resistors, the capacitor is plugged into the board from above and soldered on from below.




After soldering, cut off the wire ends again.




*Done!* This was the the warm-up. The next part is a little trickier.

=== Circuit Socket

The circuit socket has a total of 14 contact pins. That means you can now practice your soldering skills properly because all 14 solder joints are identical.




You can't miss the position of the socket on the circuit board but there is a small notch on the socket that needs to be regarded. Make sure you put in the socket with the small notch facing the Bakiwi-logo as marked on the circuit board.




When soldering, make sure that you first solder on one corner and then the diagonally opposite corner. This way you can still tare the circuit socket a little, if needed.




*Tada.* You have now already placed 22 solder joints on the Bakiwi board. If you haven't soldered so much before, then you surely have the hang of it now.

=== Button

Now look for the `PAUSE` marking on the circuit board and put in the button. If you can insert it with ease _without_ bending the pins, it is automatically the right way round. You might hear a slight click when the button snaps in.




[IMPORTANT]
====
The soldering pins of the button are a bit pointed, watch out for your fingers when inserting the button. After soldering in, you should remove these tips with pliers.
====



=== Voltage Regulator

The next component will be a little more difficult. Look for the `VREG` symbol on the circuit board. It can be found just above the orange capacitor and looks like a cut circle.




*Attention!* Now it's getting a bit fiddly. The _voltage regulator_ has three thin pins. The middle pin has to be bent so it fits onto the circuit board. You can use tweezers or a pencil, or try gently with your fingernail.



The correct arrangement of the pins is crucial for this component to function correctly. Therefore, make sure that the shape of the component corresponds to the symbol shown on the circuit board. Insert the voltage regulator and push it in bit by bit as shown. The middle leg will bend even more - that's okay.




When the voltage regulator is pressed all the way to the circuit board, it should be barely 1 mm higher than the circuit socket. Now solder the three pins as usual and shorten the wires with the pliers after soldering. You will find that the solder joints are very close together this time. Make sure that there is no short circuit.




*Well done.* Now soldering will be a little easier again, promise.

=== Battery cable sockets




Now insert the two white battery sockets at the markings `BAT1` and `BAT2`. Make sure that you insert them exactly as shown on the circuit board. The small gaps and notches on the sockets are also shown on the board. Correct alignment is very important here!




With a little skill you can insert and solder both sockets in the same operation. Here, too, it is advisable to first solder one pin and correct the alignment again if necessary.

[CAUTION]
====
Attention! At this point, please compare your circuit board with the photos shown. A battery socket that is soldered the wrong way round will later lead to reverse polarity when the battery is connected and may result in the destruction of parts of your Bakiwi. So better take a second look.
====

=== Power Switch
Continue with the power switch. It is blue/white and is placed on the board at the `POWER` marking. You can solder the switch both ways, it works equally in both directions. Just make sure it is in `OFF`-position so your Bakiwi is turned off when you put in the batteries later.




[CAUTION]
====
Too much heat melts the switch and can make it unusable, so when soldering make sure to always heat the pin and the surface around the pin at the same time so that the process is short and effective.
====




The pins of the switch are quite long and should be shortened after soldering. The material of the switch pins is a bit thicker than usual so you’ll need a little more force to snap them off.

=== Pin Headers

Now dedicate yourself to the three pin headers. The two _single-row_ pin headers (1x3) are inserted with the short end from above into the board at `MOT1` and `MOT2` and soldered to the back as usual. The motors of your Bakiwi will later be connected to them.




It is best to insert both pin headers together, then turn the circuit board and place it on the somewhat wobbly pin headers as shown in the illustration. Make sure that the pins are as perpendicular as possible to the board. If you first solder only one pin of each  header, you can correct the exact position by heating up the solder joint again, in case it should not be straight the first time.




Look for the `PROG` label on the circuit board and insert the double-row pin header (2x3) with its short end from above. Soldering in should now be easier because the two single-row pin headers now stabilize the board. The double-row pin header is the programming port in case you want to change/update the firmware of your Bakiwi later.

=== Light emitting diodes

Your Bakiwi gets two light-emitting diodes (LED) to show you the state of the walking oscillator. The position of both LEDs is marked with `D1` and `D2`. In terms of color, you can decide for yourself which LED should be on which side. You can also use different colored LEDs if you have some.




[IMPORTANT]
====

Light emitting diodes have a so-called polarity, which means that *it does matter* how they are installed. Take a look at the pins of the LED. The longer one is always the positive pole, the shorter pin is the negative pole. You can remember this if you imagine that you are mentally disassembling a plus sign and placing the lines one behind the other (`+` -> `--`). Then the plus is longer than the minus. By the way, this rule of thumb applies to all bipolar electronic components.

====




Now insert the LEDs according to their polarity and your desired color and solder them. After that, you can then shorten the pins as usual.

=== Electrolytic Capacitor

The electrolytic capacitor is installed exactly as in the previous step (long pin = positive pole). Its position on the circuit board is marked with `C2`. Make sure to put it in the right way. The negative pole is also marked with a thick (hollow) minus on the cylindrical housing.




[NOTE]
====
The color of your Bakiwi electrolytic capacitor can differ from the one in the picture, but this does not affect the function. Depending on the manufacturer, the electrolytic capacitors also have a strip of paper that stabilizes the pins. Carefully remove any paper before soldering.
====



=== Potentiometer

Your bakiwi gets four knobs with which you can change its gait. These components are called potentiometers and are adjustable resistors. You know them already from the volume knob of your loudspeakers or other devices.




Place the four blue potentiometers with the associated knobs in front of you. Insert the rotary knobs into the potentiometers with the arrows pointing upwards (according to the illustration).



Then put the assembled parts on the positions `LEVEL`, `SPEED`, `PHASE` and `BALANCE` and flip over the circuit board. The potentiometers are usually quite tight to insert and don't fall off by themselves.




Now you can solder all four potentiometers one by one. After soldering, you should also shorten the pointed ends a little.

:numbered!:

=== Take a Break

You have already soldered a lot of components. If you have worked this far, we recommend that you take a short break. Take care of yourself by getting some fresh air, drinking or eating, and most importantly, relaxing your eyes. Working in the near field can be tiring for your eyes and a little relaxation in between won't hurt.

image:./make_a_break.jpg/[width=100%]

:numbered:

=== Battery Compartments

Now you can put the circuit board aside and take the two battery compartments. There is also one red/black cable with a white plug for each compartment.

[WARNING]
====
Even if it is tempting: Please do not insert any batteries yet!
====

The cables must be soldered to the solder tabs of the battery compartments, for this you can insert the stripped cable ends into the holes. It's easier if you slightly bend the taps. Make sure the cables are facing away from the flat side of the battery compartment. This will later be the inside where the motors are and you have to avoid the battery cables getting in the way of your Bakiwis legs.

The correct polarity of the cables is of the utmost importance here. The same applies here as for the battery sockets; if  plus and minus are mixed up, parts of your Bakiwi can break. The red cable stands for plus the black cable for minus. This convention is widespread and worth remembering. You can read the polarity of the battery compartments on the inside.






Now solder the inserted cables to the very end of the tab. Solder as efficiently and quickly as possible so that the plastic of the battery compartments does not melt.

[CAUTION]
====
The plastic of the battery compartments is quite temperature sensitive. Touching the plastic with the soldering iron or heating up the solder tabs for too long can melt the battery compartment and in the worst case make it unusable.
====




=== Microcontroller

The following part does not involve soldering. You can now insert the _microcontroller_, a so-called _integrated circuit_ (or short: chip) into the socket. To do this, you first have to prepare the circuit with its 14 pins. Hold the chip as shown in the illustration and carefully bend all seven pins on each side a little further inwards. You can use the table top for that.

At first the pins point outwards a little. Ideally, after bending, they point exactly perpendicular to the chip body in the same direction. This makes it easier to insert the chip into the socket.




Now put the microcontroller in the socket, making sure that all pins are in their guides. It is important that the notch on the chip and the notch on the base point in the same direction (towards the Bakiwi-logo).




=== Antennae

The final soldering step to complete your Bakiwi board is attaching the antennae (_feelers_ or touch sensors). Your kit comes with two short pieces of guitar string. You can use them as antennae for your personal Bakiwi - but you don't have to. You can use many different metallic materials, e.g.:

* copper cable with colored insulation
* brass wire
* pipe cleaners
* or something else entirely




The sensors used are automatically adapted by your Bakiwi. It may be that they are not yet sensitive enough or even over-sensitive at the beginning. But after a few minutes, your Bakiwi will be able to use its individually designed feelers just right. So feel free to design, everything is allowed as long as it:

* can be soldered to the dedicated solder pads
* is made from mostly conductive material
* and does not touch any conductive parts of the board

*No limits are placed on your creativity.*

If you don't have any other materials available, you can also freely rearrange the enclosed guitar strings. You can attach pom-poms or bobbles on their ends. The strings are easy to solder, flexible, conductive and are quite robust and do not kink easily. Here are two examples:




For soldering, place the circuit board with the components facing up on the table and first solder the sensors to the top of the circuit board and then to the back as usual. This gives you better control over their alignment.

[NOTE]
====
Remember, there may be more metal to heat up for your soldering iron than usual, so you may have to hold the soldering tip on for a few seconds longer. The large soldering areas and the thick wire absorb a lot of heat and get hot, watch out for your fingers!
====




== After Soldering

=== Clean Up

*Drum roll.... cymbal strike.* You've done it. The soldering work is now complete. The soldering station is no longer needed and you can turn it off and let it cool down.

[WARNING]
====
The solder tip can be very hot for a few minutes after it has been switched off. So let the soldering station cool down for a while before you put it away.
====

Finally, we recommend equalizing the solder joints on the back again and shortening the remains of the pins that are too long. This is important so that after the mechanical assembly there are no more pointed pins that could dig into the motor or battery cables.




=== Waste Disposal

We tried to design the kit so that there is as little waste as possible. Please separate the waste and recycle. All small metal residues can be disposed of as packaging waste and the scraps of paper as waste paper. If you like, you can reuse the enclosed zipper bags and the cardboard box or dispose of them as packaging waste or waste paper.

=== Testing
In case you have a multimeter at hand: Before the mechanical assembly begins all electronic components should be tested. This way you could identify potential short circuits.

==== Short Circuit Test




Take a multimeter and switch it to continuity test mode ("beeper"). You can recognize this by the loudspeaker symbol. Hold the two test probes with the metallic ends against each other and make sure that there is a clearly audible beep. The beep sound signals an electrical contact with no significant resistance in between. You can use it to check solder joints, cables and plugs for proper contact or to find unwanted short circuits.




Now hold the test probes on the two pins of the left battery socket. No signal should sound here. Repeat the test with the other socket. Also test the pins of the two motor connections and the 6-pin programming port by checking each two adjacent pins for short circuits. If there is a beeping for two pins, you have to look very carefully at your solder joints at this point. It is possible that some solder has gotten between the solder joints and is connecting them. Make sure there is enough light during the inspection and, if necessary, use a magnifying glass.

[TIP]
====
If two solder joints are accidentally connected with solder, you can try to separate them by reheating them. If the solder looks sticky, try adding some fresh solder (with flux that has not yet evaporated) to make the solder joints workable again. The colored varnish (blue or purple) on your circuit board will not accept solder and will help you separate the solder joints. If both joints are heated up together and have sufficient flux, they separate easily from each other and retreat to their solder pads.

Optical inspection can also rule out many possible sources of error. A good solder joint always looks a bit like a small volcano or mountain, if the solder joint looks more like a ball, this can be evidence that too little solder has landed on the pad. In this case the contact might be not reliable.
====



Finally, test the positive pole of the left battery socket against the negative pole of the right battery socket. There should also be no contact to be measured here. Set the power switch to `ON` and measure again. There should now be a contact and you should hear a beep when measuring. Now turn the switch back `OFF`.



==== Connect Motors
[#connect_motors]

Now connect the motors. Make sure that the brown (or black) wires of the 3-wire motor cable are connected to the pin that is marked with the ground symbol on the circuit board (see illustration).




Now insert the batteries. It is very important to note the polarity (+/-) displayed inside the battery compartment. The plus and minus symbols can also be seen on your batteries or rechargeable batteries. Now connect the battery plugs to the sockets on the circuit board, it doesn't matter which compartment you connect to which plug.




[WARNING]
====
*Watch out!* If the batteries get warm or even hot after connecting the compartments, you have to disconnect the connector from the circuit board immediately. The heating up of the batteries very likely indicates a short circuit and you will have to repeat the electrical continuity test again and carefully inspect your solder joints to find the short circuit.
====

Now turn `ON` the power switch and if everything is put together correctly, you should already see the diodes flashing. When all rotary knobs with the arrows point upwards, the LEDs should flash in unison.

If the diodes work, press the button and immediately afterwards both motors should start making noises and turn the shafts (the round toothed metal ends).

Touch the feelers with your hands and the noises of the motors should immediately change, slow down or even stop. When the sensors are released, the motors should resume their original behavior. Now turn your Bakiwi off again.

If everything works as expected so far, you can now move on to the next chapter, the <<assembly, mechanical assembly>>.

If only one motor works but the other does not, make sure that all knobs are pointing up and that the motor cables are connected as described in the section <<connect_motors, Connecting Motors>>.

=== What to do when something is broken?

If you should have lost or broken a component during soldering or assembly: Don't panic! We'll be happy to send you a new one. Send us a letter with the broken part and a return envelope addressed to you and we will arrange for a replacement immediately. We would be happy if you take the time and briefly describe to us how the component broke so that we can improve our Bakiwi kit with your help.

If there is a problem but you are not entirely sure what is causing it, you can also send us photos of the board (e.g. from the top and bottom side) and we can try to help identify the source of the error.

== Mechanical assembly
[#assembly]

:imagesdir: ./img/02_mechanics/

=== Preparation

Take the illustrated mechanical components out of the package and place them in front of you. You have already prepared the Bakiwi circuit board and the battery compartments in the previous work steps.



You will need additional tools for the assembly: a small Phillips screwdriver and a hexagon socket screwdriver (2.5 mm). If available, tweezers may be useful and simplify the assembly, but they are not strictly necessary. The side cutter is also required again.



=== Install Motors

We start our mechanical assembly with the motors. To do this, take one of the motors and a motor holder as well as two of the four Phillips screws (you can recognize them by the fact that they are the only ones with tips). Fold the motor cable a few times, as shown, and squeeze it gently so that it falls into the same folds more easily when you install it.




Thread the motor cable through the large opening in the holder and out of the holder again through the small opening on the side. Now insert the motor into the holder. Make sure that part of the cable is folded in the holder so that less of the cable protrudes overall. The shaft of the motor should point away from the small opening (compare your result with the picture).




Now insert the screws one after the other and tighten them sufficiently. If everything is in place, repeat the steps with the second motor.




=== Putting the frame together

Next, put the frame together. To do this, place the base plate of the frame in front of you and place the V-shaped clamp nut between the two central hole bars. Insert the locking screw and tighten it two turns.




Place the two motor holders with their axle ends on the holes in the base plate. Make sure that the openings and protruding cables are facing up. Now put on the lid of the frame and hold everything together with your fingers. If you gently tighten the locking screw a little further, the frame will hold together better.




==== Thread and stow the cables

Hold the frame so that one motor is pointing to the left, the other is pointing to the right, and the cables stick out upwards. Now thread the motor cable on the left side of you through the rear hole facing away from you. The right-hand motor cable goes through the hole facing you.

Stow the two motor cables in the frame above the clamp nut so that about 4 cm of cable protrude from the frame.




==== Mounting the circuit board

Now you need the two cylinder head screws (M3x10mm) and the hexagon socket screwdriver. One after the other, insert the screws into the holes in the Bakiwi board and screw them onto the frame.

[TIP]
====
With a bit of luck, the screws can be attached to the hexagon socket screwdriver and are held there by friction; some tools are also magnetic. This usually makes it easier to insert the screws into the holes in the board.
====

[NOTE]
====
Attention, when screwing in for the first time, the screws cut their own thread into the holes in the frame base plate. If you want to loosen and reinsert the screws later, try to _feel_ the thread by turning the screw slightly to the left before tightening it until it fits into the original thread.
====



The frame will now hold together by itself, carefully tighten the locking screw a little further with your fingers and test how the motor holders can now be locked in into certain positions.

=== Connect the Motor Cables

Now the motors are wired. We already had this step during testing, make sure again that the brown (or black) wires of the motor cables point to the ground symbol (see section  <<connect_motors, Connecting Motors>>). Stow the two motor cables as far as possible in the frame so that they fit snugly and do not form large loops.




=== Attach battery holder

==== Preparation

Now prepare to attach the battery holders. You need the four M3x4mm cylinder head screws, the hexagon socket screwdriver and the side cutter.



First remove the two spacer bars in both battery compartments by separating them just above the surface. Now screw the battery compartments to the side of the frame. There is now enough space for the screw heads.




==== Mounting

The battery compartments should be positioned so that the cables are on the side with the sensors. Each holder is fixed to the frame with two screws. Here, too, the screws cut their threads into the holes in the frame the first time they are inserted.

[CAUTION]
====
*Warning!* Be careful not to overtighten the screws.
====



==== Stow the battery Cables

Lay the battery cables behind the motor cables along the circuit board to the rear and plug them into their sockets. If necessary, carefully slide the cable under the circuit board.




*Hooray!* Your Bakiwi's body is finished now. Double check the alignment of the connectors on your circuit board and whether all cables are as close as possible to your Bakiwi’s body.



=== Attach Legs

First put the batteries back in and switch on your Bakiwi. Press the `PAUSE` button twice in succession with an interval of about one second so that your Bakiwi moves its motors to the starting position and then goes back to pause mode.




Now mount the leg connections onto the toothed ends of the motors' shafts and screw them tight with the enclosed Phillips screws. It's the last two screws that are left.

The enclosed 3D-printed leg connections are just one of countless ways to put legs on your Bakiwi. In your kit there are perhaps other parts that fit on the shafts of the motors (so-called horns).

*Give yourself a try!* With the remaining horns you can make different pairs of legs from different craft materials and switch over and over again.
//TODO link to the leg building manual




*Done!* Depending on which Bakiwi kit you have, there may be small Lego parts included, which can be used as feet for your inital Bakiwi. Maybe you already have Lego Technic parts. You can use these to design legs and feet for your bakiwi very quickly.



== How to play your bakiwi and how it works

=== Before Switching on

*Important:* Before switching on for the first time (with the legs attached) take a closer look at the names of the four gray knobs (potentiometers).

. Set the `BALANCE` and `PHASE` controls to the middle position (arrow upwards).

. Set the `SPEED` control halfway to the left (toward the long waveform).

. Set the LEVEL control halfway to the left (toward the small waveform).

Now turn on your Bakiwi.

=== The Functionality Explained

:imagesdir: ./img/04_usage/

OSC

In the program memory of your Bakiwi microcontroller there are two neurons that form an oscillator which create the clock signal for the movement of the legs. The two LEDs on your Bakiwi signal the activity of these motor neurons. In the pause mode, the neurons and thus the oscillator are already active and swing, but the motors are inhibited. This means that you can change the movement pattern at any time by adjusting the four knobs, whether paused or not.

We recorded a video to better illustrate how it works:

ifdef::env-github[]
link:https://youtu.be/rAteGra5-xM[Direct link to the video^]


endif::[]

ifndef::env-github[]
video::rAteGra5-xM[youtube, width=640, height=360]
endif::[]

=== Gait Parameters

The way your Bakiwi walks is influenced by several factors. The legs that you create for your Bakiwi are decisive for successful locomotion. If you have come up with new legs for your Bakiwi, you can teach it to walk with them by changing the following parameters:

==== Motor Joint Angle

The motor joint angles are purely mechanical parameters. You can make the motor mounts movable by loosening the large locking screw and then changing their angles to the body and to each other. *Try different angles and watch the difference it makes!* Tighten the screw again only until the motor mounts hold firmly enough in the desired position.

==== Speed/Walking Frequency

SPEED

The frequency regulates the walking speed of your Bakiwi. Turn the `SPEED` knob and watch the LEDs change their rate of blinking. Leave the pause mode by pressing the button and observe the motors. Turn the knob back and forth and see how the motor neurons' oscillation speed changes the gait frequency and influences your Bakiwi's walking speed.

[TIP]
====
We recommend starting with a slow movement first. It helps you to be able to observe the movement of your self-made legs and thus to get a good understanding of the locomotion.
====

==== Level/Amplitude

LEVEL

Turn the `LEVEL` knob and watch how the brightness of the LEDs changes and how far the motors deflect with every movement. In terms of oscillations this is called the amplitude and controls the step size of your Bakiwi's gait.

==== Balance

BALANCE

Turn the `BALANCE` control and watch how the previously set amplitude is distributed between the two motors. If the controller is in the middle position, both motor amplitudes are the same. Turning to the left decreases the amplitude of the front motor, turning to the right dampens the movement of the rear motor.

==== Phase

PHASE

The last parameter, the so-called phase (or the phase angle) is truly the special flavor and controls the direction of movement. 
A `PHASE` controller in the middle position produces a synchronous but opposite movement of the motors. If you turn the phase angle a little out of the middle, the motors no longer move synchronously, which is crucial for walking. A phase angle set up to the maximum (or minimum) again generates a synchronous but this time concurrent movement. The phase is the most important parameter for a successful walking movement and needs your special attention. The phase setting will decide whether your Bakiwi will move at all and if so in which direction.

But read enough now ...

*Get to work! :)*

=== Centering

When you have assembled your Bakiwi, you should center  its legs if necessary. The motors with the attached leg connections are never perfectly straight due to the manufacturing process. Your Bakiwi can correct this offset and remember it.

To do this, first turn off your Bakiwi.

. Hold down the pause button and switch on your Bakiwi while holding the button. Both LEDs should now flicker quickly.

. Release the button and now only the left LED should flicker and the front motor should start up briefly. If you now turn the `PHASE` knob you can set the front motor to the desired zero position. Adjust until the leg connection is straight enough.

. Press the button again to confirm. While the right LED is now flickering, you can repeat the process for the rear motor.

. If the rear motor is also correctly adjusted, confirm again by pressing the button and the centering process is now complete.

[TIP]
====
If you are building new legs for your Bakiwi and the legs, whether intentional or unintentional, are not symmetrical you can also use the centering method to compensate for any offset.

But you can also use it specifically to let your Bakiwi always run a curve.
====

=== Schematics

Below you can see the circuit diagram (schematics) of your Bakiwi. Can you find out for yourself which symbols belong to which parts you soldered? _Reading_ a circuit diagram takes some practice, but now that you have soldered all the parts together yourself, you can see here which component is wired to which. The cables on a circuit board are called _tracks_ and consist of a thin layer of copper. If you look at the circuit board of your Bakiwi and hold it slightly up to the light, you can see them under the layer of varnish. Some tracks change the side of the board through small holes, so-called _vias_. Some  tracks are also whole areas, for example the entire bottom copper area of the board is the negative pole.

A circuit diagram also helps with troubleshooting. If the electronics behave strangely, a multimeter and a circuit diagram are the most important tools in finding the cause. The components are also precisely identified in the circuit diagram. There you will find, for example, the resistors' values, the capacitance of the capacitors, the forward direction of the diodes or what the name of the voltage regulator is. With the help of a circuit diagram, an electrical device, like your Bakiwi, can be repaired over and over again.

:imagesdir: ./img/


:numbered!:

== Do you have any questions?

Do you have any questions or would you like further explanations? Do you have any suggestions or feedback for us? link:https://jetpack.cl/bakiwi[Write us!]

You can also follow us on Twitter, there we will provide you with news about *#bakiwi*. We are link:https://twitter.com/labjetpack[@LabJetpack].

Otherwise we wish you a lot of fun with your new Bakiwi. Let it crawl!

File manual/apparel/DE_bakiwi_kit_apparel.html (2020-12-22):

# Bakiwi-Mode-Nähanleitung

Doc Writer
kubisch@informatik.hu-berlin.de
version 0.1, 2020-12-16

Anleitungstext, Vorlagen und Fotos von Karen Ellenmeyer

fur colors

Übersicht

- Vorbereitung
  - Werkzeuge
  - Materialien
- Schnittschablone erstellen
- Stoff falten und Schnitt anzeichnen
- Stofflagen zuschneiden
- Löcher stanzen und verstärken
- Nähen
- Saum umlegen und befestigen
- Anprobe

## Vorbereitung

Für das Schneidern der Bakiwi-Bekleidung benötigst du folgende Werkzeuge und Materialien:

### Werkzeuge

- Nähmaschine (empfohlen)
- Lochzange
- Nähnadel
- Stecknadeln
- Haushaltsschere
- Bleistift
- Maßband oder Lineal

### Materialien

- Stoffstücke mit leichter Dehnung
- Garn
- Alleskleber

💡 | Falls du noch gar keine Erfahrung im Nähen hast, schau Dir ein paar Tutorials im Internet an oder lasse Dir von Freunden oder Verwandten etwas zeigen bzw. frage Sie, ob Sie dich beim Nähen und Bedienen der Nähmaschine etwas anleiten können.

## Schnittschablone erstellen

Erstelle Dir eine Schnittschablone, indem Du wahlweise die Zeichnung selbst auf Papier bringst oder die Vorlage (PDF) auf Papier oder Folie ausdruckst. Wenn Du einen 3D-Drucker hast, kannst du auch unsere Schablonenvorlage (STL) 3D-drucken. Die angegebenen Maße sind für Stoffe mit leichter Dehnung.

❗ | Die angegebenen Schnittschablonen und Maße sind für Stoffe mit leichter Dehnung dimensioniert (blaue durchgezogene Linie). Wenn du sehr feste Stoffe ohne merkliche Dehnung verwenden möchtest, empfehlen wir, die Schablone umlaufend ca. 7 mm größer anzufertigen (gestrichelte Außenlinie).

cut drawing 00 get stencil

## Stoff falten und Schnitt anzeichnen

Falte den Stoff so, dass die rechten Seiten (Fell) innen liegen und die linken Seiten außen sind. Achte darauf, dass die meiste Dehnung des Materials in Querrichtung ist. Wenn Du Fell-ähnliche Stoffe benutzt, achte darauf, dass der Strich nach unten zeigt, d. h. dass es in Richtung Saum glatt gestrichen werden kann.

Lege die Schnittschablone auf und zeichne den Schnitt mit Bleistift oder Kreide auf der linken (d. h. inneren) Stoffseite an. Vergiss dabei nicht, die Positionen für die Sensoren zu markieren!

01 prepare 02 mark

## Stofflagen zuschneiden

Stecke beide Lagen mit ein paar Nadeln zusammen, damit sich die Stofflagen beim Zuschneiden nicht verschieben. Schneide dann beide Lagen zusammen möglichst genau auf der Linie aus.

03 cut 04 mark holes

## Löcher stanzen und verstärken

Mit einer Lochzange kannst du jetzt die Löcher für die Sensoren durch beide Stofflagen stanzen. Am besten legst du ein Stück Pappe beim Stanzen mit darunter, zwischen den Stoff und die Auflage, dann lassen sich die Löcher schön sauber ausstanzen.

Sichere nun die ausgestanzten Öffnungen mit etwas Klebstoff vor dem Ausfransen, ein Allzweckkleber sollte dafür genügen. Nimm eine Nadel oder einen Zahnstocher zur Hilfe, um den Kleber vorsichtig im Radius von etwa 3-4 mm um die Löcher herum zu verteilen. Lasse den Kleber ausreichend lange trocknen.

05 cut holes 06 reinforce holes

## Nähen

Nähe jetzt füßchenbreit mit der Nähmaschine um die Schnittkanten herum. Vergiss nicht am Anfang und Ende die Naht zu verriegeln, d. h. nähe hin und zurück, damit Sie nicht aufgehen kann.

07 sew

## Saum umlegen und befestigen

Lege den Saum 2 cm um und befestige ihn mit dem Überwendlichstich (d. h. mit doppeltem Faden) von Hand. Alternativ kannst du ihn auch festkleben. Achte aber darauf, nicht zu viel Klebstoff zu verwenden, damit er nicht auf die rechte Seite des Mäntelchens durchschlägt.

08 measure 09 sew the hem

## Anprobe

Wende Dein neu-geschneidertes Fell und kleide Dein Bakiwi an. Dabei sollten die Fühler zuerst durch die Löcher im Fell gesteckt werden.

Fertig! Tadaahhhh.

Wenn Du möchtest, sei so gut und schicke uns ein Foto oder Video von Deiner Kreation an info@jetpack.cl für unsere Sammlung oder poste Deine individuelle Bakiwi-Mode mit dem Hashtag #bakiwi.

10 ready made 11 done

Version 0.1
Last updated 2020-12-22 23:43:20 +0100

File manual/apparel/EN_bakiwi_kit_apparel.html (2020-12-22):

# Bakiwi Apparel Sewing Instructions

Doc Writer
kubisch@informatik.hu-berlin.de
version 0.1, 2020-12-16

Instructions, templates and photos by Karen Ellenmeyer

fur colors

Contents

- Preparation
  - Tools
  - Materials
- Create the template
- Fold the fabric and mark the cut
- Cut out the fabric
- Punch holes and reinforce
- Sewing
- Turn the hem up and fasten it
- Try on

## Preparation

You will need the following tools and materials to tailor Bakiwi clothing:

### Tools

- sewing machine (recommended)
- punch pliers
- sewing needle
- pins
- scissors
- pencil
- tape measure or ruler

### Materials

- pieces of fabric with light stretch
- yarn
- all purpose glue

💡 | If you have no sewing experience at all, take a look at a few tutorials on the Internet or let friends or relatives show you some sewing, or ask if they can teach you how to use the sewing machine.

## Create the template

Create a cutting template by either sketching the given drawing on paper yourself or printing out the template (PDF) on paper or foil. If you have a 3D printer, you can also 3D print our stencil. The dimensions given are for fabrics with light stretch.

❗ | The specified cutting templates and dimensions are made for fabrics with slight stretching (blue solid line). If you want to use very firm fabrics without noticeable stretching, we recommend making the template approx. 7 mm larger all around (dashed outer line).

cut drawing 00 get stencil

## Fold the fabric and mark the cut

Fold the fabric so that the right sides (fur) are on the inside and the wrong sides are on the outside. Make sure the material’s most stretch is is in cross direction. If you are using fur-like fabrics, make sure that the direction of the hair is facing down, i.e. that it can be smoothed towards the hem.

Put on the cutting template and mark the pattern with a pencil or chalk on the wrong (i.e. inner) side of the fabric. Don’t forget to mark the positions for the sensors, too!

01 prepare 02 mark

## Cut out the fabric

Pin both layers together with a few needles so that they can’t move whilst cutting. Cut them out on the line, both at the same time, and as precisely as possible.

03 cut 04 mark holes

## Punch holes and reinforce

Use punch pliers to cut holes for the sensors through both layers of fabric. For best results when punching, put a piece of cardboard below, between fabric and support surface. then the holes can be cut out nice and clean.

Now secure the holes from fraying with a little glue. All-purpose glue should suffice. Use a needle or toothpick to gently spread the glue around the holes in a 3-4 mm radius. Let the glue dry long enough.

05 cut holes 06 reinforce holes

## Sewing

Sew around the edges foot width on your sewing machine. Make sure beginning and end are locked by sewing a few stitches back and forth.

07 sew

## Turn the hem up and fasten it

Fold the hem 2 cm up and sew it by hand, going over the edges with double thread (overlock stitch). Alternatively, simply glue the hem all the way around. Make sure not to overuse the glue so it can’t bleed through to the right side of the fur.

08 measure 09 sew the hem

## Try on

Turn over your newly created fur and dress up your Bakiwi. The feelers should first be inserted through the holes in the fur.

Done! Tadaahhhh.

If you like, please be so nice and send us a photo or a video of your creation to info@jetpack.cl for our collection or post your individual Bakiwi apparel with the hashtag #bakiwi.

10 ready made 11 done

Version 0.1
Last updated 2020-12-22 23:09:28 +0100

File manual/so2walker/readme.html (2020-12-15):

# Bakiwi Assembly Documentation

Doc Writer
kubisch@informatik.hu-berlin.de
version 0.2, 2020-04-02

This is the old Bakiwi’s assembly manual. If you bought your Bakiwi after June 2020 you are probably looking for the new manual. With the following steps you can assemble your Bakiwi walking robot from the kit. We encourage everyone to contribute to this project. Please share your ideas and experiences, upgrades and schematics, source code and tricks.

title

## Motivation

There is some video links available on how Bakiwi could look like when assembled and how it performs.

video: bakiwi robot with lego legs (https://www.youtube.com/watch?v=UyHHptdRnA0)

video: bakiwi robot with spring steel legs live at xHain hack+makespace (https://www.youtube.com/watch?v=lXEHFaAaYYs)

Table of Contents

- Motivation
- Preparation
  - Prepare Workbench and Tools
  - Recommended Tools
  - Check the Parts
  - Bakiwi Assembly Kit Parts
- Soldering
  - Prepare Soldering
  - Solder Nano-Board Header
  - Resistors
  - Capacitors
  - LEDs
  - Switches
  - Socket
- Get a break
- Soldering (continue)
  - Servo Header
  - Potentiometers
  - Battery Pack
  - Soldering finishing
- Testing and Flashing Firmware
  - Insert Batteries
  - Installing Arduino IDE
  - Checking out the Code-Repository
  - Compile Firmware
  - Connecting the Nano-Board to a PC
  - Selecting Board and Microcontroller
  - Uploading Firmware
  - Testing the Functions
- Assembly

## Preparation

Note | Before starting the assembly. Check that you have all the tools and parts in place. We recommend reading this manual once briefly before starting the assembly. Please also have a look at the schematics of the board or the board’s layout.

01 package

### Prepare Workbench and Tools

Clean and wipe your workbench and get all the tools needed as denoted in the list or shown in the picture.

### Recommended Tools

We recommend these tools to assemble the Bakiwi robot:

- soldering iron with a very fine tip and solder (0.5mm) and up to 400°C (regulated) temperature
- flat-nosed pliers
- side-cutting pliers
- wire stripper
- utility knife
- multimeter
- sandpaper or files
- small Phillips screw driver
- tweezers (optionally)
- hot glue or superglue (optionally)
- a box of craft materials, trash or old Lego parts for creating legs and body parts of your robot.

02 tools

### Check the Parts

Tip | Check the parts in your Bakiwi package for completeness and complain to me via email if it’s not complete :)

### Bakiwi Assembly Kit Parts

2 | micro servos (incl. several horns)
4 | mini-potentiometers 10 kΩ
4 | mini-knob
1 | PCB SO(2)-Walker (referred to as the motherboard)
1 | Arduino-Nano compatible board (i.e. Nano-Board)
2 | battery holder (2xAA)
2 | 1 kΩ resistor
2 | LED (two different colors)
4 | 1x3 pin header
2 | 1x15 socket
1 | 100 µF electrolytic capacitor
1 | 100 nF ceramic capacitor
1 | tactile button
2 | on/off slide switch
4 | 10 cm cable

03 parts

Important | Batteries might not be included in the set. Ask your workshop leader or get you a set of 4x AA (mignon) batteries with 1.5 Volts each.

batteries not included

## Soldering

### Prepare Soldering

Prepare your workbench for soldering. We recommend using a fine tip and thin solder.

Important | Watch your health! Use enough light. Make sure there is fresh air during soldering and not to breath-in the solder vapor.

Caution | Soldering irons get REALLY hot. You need to stay focused and should be careful not to burn yourself or others. When leaving the table or room, switch off the soldering station.

use fine solder tip

Adjust the soldering station for sufficient heat depending on the solder you use. Some stations show the current temperature, make sure to let the iron pre-heat before starting. If soldering 'feels' very sticky, you might have not the correct temperature (too cold) or the flux in the molten solder has already evaporated. Also, ensure to always use a clean solder tip, preferably using a dry cleaner (metal pot cleaner) as it does not cool down the solder tip (in comparison to a wet sponge) and the cleaning result is generally better.

solder with enough temperature

Keep the electronic parts together as they are tiny and get lost easily when they are accidentally dropped from the table.

keep parts together

### Solder Nano-Board Header

So now you should be prepared for soldering the first part. Insert header pins for the Nano-Board as shown in the picture.

insert pinheader

You can use a breadboard, if available, for stabilizing the pin headers and keep them aligned and perpendicular during soldering.

use breadboard if available

Solder the pins one after another. After soldering the first pin, double-check for alignment and correct it if needed. Otherwise, continue soldering all 30 pins.

solder nano pins

The result should look like this. Sufficient solder looks shiny and volcano-shaped. If it looks like a water drop or ball then there is too much solder. You can remove it by cleaning the tip and put the soldering iron again to the pin. Alternatively, use de-soldering braid to remove excessive solder.

If the solder point has a weird shape or noses, then there was probably not sufficient flux available in the melting process, use a little fresh solder to make the solder point shiny again.

nano solder result

### Resistors

Get the two 1 Kilo-Ohms resistors and the motherboard. Don’t get irritated as the color might be different than shown in the picture.

parts resistor

parts so2walker

Bend down the resistors' leads very close to their ends and trim the leads as shown in the picture.

bend cut resistor

Insert resistors as depicted and printed as R1 and R2 on the board’s silk screen. Make sure that the resistors are soldered very closely to the board.

insert resistor

Trim the leads after soldering using the side-cutting pliers.

solder resistors and cut wire

### Capacitors

Get the two capacitors. They completely differ in size and form.

parts capacitors

Insert the ceramic capacitor (small) first as it has a lower profile. Again, make sure that the capacitor is soldered very closely to the board.

insert ceramic cap

The electrolytic capacitor has a polarity and its leads must not be mixed up. The shorter lead is minus, the longer lead is plus. Make sure polarity is correct as denoted on the board and shown in the picture. The capacitor must be laid on its side since the Nano-Board will be mounted above it.

insert electrolytic cap

### LEDs

Get the LEDs. Their colors or shape can be different depending on the version of the assembly kit.

parts leds

The LEDs also have polarity. Again, the shorter lead is minus, the long lead is plus. Make sure polarity is correct as denoted on the board and shown in the picture.

Note | To remember which lead is plus or minus, imagine, there is a rule of thumb: The dashes of the plus sign put together in a line are longer than the minus dash. Easy, isn’t it?

insert leds

### Switches

Get the switches. The silver/black one is a tactile switch, a button so to say. The other one (blue/white) is a slide switch.

parts switches

Insert and solder the slide switch and button. When inserting the tactile button, look out for correct orientation. There is only one correct way and you probably need to gently press the part into the board. You feel a little click when inserted correctly. The orientation of the slide switch is pretty clear and can be installed in both ways. After soldering, make sure that the slide switch is turned off (as marked on the board).

insert slide switch

### Socket

The next thing to solder is the sockets for the Nano-Board. The sockets in your package might have more than 15 slots, so you need to trim the socket to exactly 15 slots and use sanding paper to make it even. Be careful when trimming the sockets, they might break easily. You have to cut directly through the 16th socket pin, not between pins as this might accidentally break the 15th pin as well.

cut socket

sand socket cut

Then insert the socket and solder the 30 pins. For each half of the socket, make sure the sockets are aligned perpendicular and closest to the board. Otherwise, the Nano-Board might not fit into the socket.

insert sockets

## Get a break

Note | Now it’s time to grab a coffee or similar and relax your eyes. Get some fruit and fresh air, give your body a break :)

make a break

## Soldering (continue)

Hope you are relaxed, now :)

### Servo Header

Get the servo pin headers and insert four times the 1x3 pin servo header to all four corners of the board, next to the screw holes. Again, make sure the pins are perfectly perpendicular to the board, otherwise, the servo connectors might interfere with the sockets of the Nano-Board.

insert servo pin header

### Potentiometers

Get the four potentiometers (10 KOhms) and the associated knobs (might have a different color) and insert the knobs in such a way that the shiny metal part of the potentiometer is on the back. When inserting the knobs, make sure the arrow is pointing upwards. Check for correct neutral position (pointing to the top), e.g. when turned fully to the left end stop the arrow should point in the lower left corner and when turned fully to the right end stop, the arrow should point to the lower right corner.

prepare potis

Insert the potentiometers as shown in the picture, turn the board and solder them.

insert potis

### Battery Pack

Get the wires (approx. 10 cm each). The might have different colors than depicted or the wires come as a flat cable.

get wires

Strip the insulation of all the wires' ends, approx. 3-5 mm, twist the ends a little and pre-solder the wires. Pre-soldering is useful to better insert the wire into solder holes.

strip wire and presolder

The result could look like this.

wires result

Insert the wires in the denoted order and solder them to the board.

wire order

Twist pairs of wires, each pair will be associated with a single battery pack of two cells. If you have a flat cable, you can split them in two pairs of wire.

twist wire

Turn the leads of the battery pack a little upwards so they do not stick out over the part.

battery pack turn leads upwards

Check polarity of the battery pack (it is denoted inside the packs).

polarity batterypack

Solder wires to the battery packs as shown. Double check for correct polarity. According to your cable colors the order should be (B1- B1+ B2- B2+) with Bx denoting the battery pack (1 or 2), as denoted on the board/schematics.

Caution | Battery packs are made of temperature-sensitive plastic. Try to solder only as short as possible in order to avoid melting the plastic. This could irreversibly damage the pack and lead to connection problems later.

battery pack soldered wires

### Soldering finishing

So, congratulations. You did it. You finished soldering. Yay. \o/

Next thing to do is to trim the pins to be as short as 1-1.5 mm.

cut pins short

Dispose the trash material correctly. Metal, plastic and paper parts can be recycled and should not be put to residual waste.

dispose solder waste

Note | Do not dump the bags. Re-use them or return them to your workshop leader if you do not need them anymore. Save resources. There is no planet B, right?

reuse plastic bags

## Testing and Flashing Firmware

multimeter

Before installing batteries, get your multimeter and check at least for three things:

- Use the short circuit detection mode (beep mode) and check whether there is good connection between the battery packs and the board. Measure from the very end (e.g. the spring in the pack) to the wire end soldered to the board. The multimeter should make a beep sound here signaling a proper (low-resistance) connection.
- Next check the four battery cable ends for possible cross connections. There should be none (if you nonetheless find a short circuit between the inner cables, make sure that the power switch is in off position). Remove any short circuits. Check (optically) for possible short circuits on all your soldered connections on the motherboard and Nano-Board. If unsure, check (electrically) with the multimeter.
- The last thing: Check electrically (!) for potential short circuits between GND, VIN and +5V as denoted on the Nano-Board pins.

Please be careful with this last step and make sure that there is no short circuit (left) as this can destroy components of your robot irreversibly. In any case, if some component of your robot is getting hot, remove batteries immediately and check for potential problems. Maximally the motors are getting warm after longer use, the rest of the robot should stay at environment temperature.

### Insert Batteries

Now it is time to first power-up your freshly soldered Bakiwi robot.

- Make sure the power (slide) switch is in "off" position.
- Insert the Nano-Board into the sockets of the motherboard with the USB connector turning pointing towards the tactile switch.
- Insert all four batteries into the holders according to the polarity denoted inside the battery holders and the batteries themselves.
- Switch the power on and the Nano-Board should be light-up its onboard LEDs.

### Installing Arduino IDE

Get a computer and browse to https://www.arduino.cc/en/Main/Software and download and install the latest Arduino IDE according to the description on the Arduino website. If you already worked with Arduino boards and have the IDE already installed on your computer, you might consider updating to the current version as it might be required to detect the Bakiwi robot’s control board in the Arduino IDE. This manual was tested with version 1.8.8 without any problems or modification needed.

### Checking out the Code-Repository

Download the latest Bakiwi firmware source code folder with name so2walk from https://github.com/ku3i/Bakiwi.git and save to your local hard drive (hit the Clone or Download button on the Github website).

Alternatively, if you are familiar to a Linux terminal and want to use the source code version system Git, type

git clone https://github.com/ku3i/Bakiwi.git

to clone the code repository to your computer. Optionally, if Git is not already installed on your Linux machine, type

sudo apt install git

If you have question on using Git (e.g. for other operating systems), please refer to https://www.git-scm.com/.

### Compile Firmware

Open the Bakiwi firmware’s source code in the Arduino IDE (file→open) and hit the compile button (it looks like a checkmark, it’s somewhere in the left upper corner). When compiling works without complains from the IDE then all the code dependencies seem to be fulfilled on your machine and the compiler was able to create the binary code to be run by the microcontroller on the Nano-Board. The firmware source code file is located in:

Bakiwi/source/so2walk/so2walk.ino

### Connecting the Nano-Board to a PC

Remove batteries again and connect the Nano-Board to your computer via USB (mini)-cable. The board should immediately power-up again as you connect the cable.

connect nano to pc via usb

### Selecting Board and Microcontroller

Next you need to select the target board and processor. The Nano-Board is compatible to Arduino Nano and hosts an 8-bit ATMEGA328p microcontroller. After setting the board via Tools → Board → Arduino Nano you also have to select the correct microcontroller and Bootloader combination via Tools → Processor → ATMEGA328P (Old Bootloader). If the old-bootloader option is not available in your Arduino IDE you may consider updating to the current version.

Please note: The board uses an USB-to-Serial chip-set called "CH340" which, depending on your operating system, may need some sort of driver to be installed.

arduino IDE

### Uploading Firmware

You can now upload the code by hitting the upload button (an arrow to the right). If everything has worked out fine, the motherboard’s LEDs should blink in a periodic pattern.

### Testing the Functions

For testing, follow these steps:

- remove the USB cable
- make sure robot is switched off
- connect motors (yellow cable pointing towards the knobs)
- insert batteries
- check all knobs are in neutral position
- switch on

The LEDs should again be blinking periodically. The four knobs modify the properties of the neural oscillator: Frequency, Phase and Amplitude (2x).

There are four 3-pin headers that allow for connecting motors. In the current version of the code only two of them are sending motor commands (the two next to the USB connector). The others you can use for connecting additional motors or sensors, when you modify or extend your robot or its code.

You find the knob which modifies the frequency in the right upper position when holding the board with the USB connector upwards while looking from the Nano-Board side. Try out modifying the frequency and watch the LEDs blinking accordingly. The blinking LEDs corresponds to moving motors later. So the motors will change direction with the same frequency as shown by the LEDs.

For each motor the oscillation is tapped at two different positions, so that you can create patterns that are either more in-phase or anti-phase. The right lower knob modifies the phaseshift between those taps. Try out the phase knob and so how you can create different blinking patterns.

When powering-up, your Bakiwi is in pause mode. You can now start the motors by hitting the tactile button. The motors will now begin to move according to the frequency and phaseshift you set.

The other two knobs (on the left side) can be used to modify each motor’s amplitude. You can either decrease the amplitude by turning them to the right until the motors fully stop or you can increase the amplitude to a certain maximal value by turning them to the left.

Please note that a mixture of large amplitude and high frequency at the same time can probably not be accomplished by the motor since every physical device has some sort of inertia.

install nano board and connect motors

## Assembly

We’re sorry. The assembly manual for the development version of Bakiwi ("SO(2)Walker") ends here. How you create your robot’s body is at the moment up to you for this version. However, the given pictures suggest how you can proceed. Try fixing the motors with double-sided tape first and try mounting them in some different angles. If you’ve found a working (and walking) solution then you may use permanent glue to attach the battery packs to the motors. The board can either by temporarily mounted with a rubber band or fixated with hot glue. Also using the surplus screws inside the motors' packaging is an option.

Let us know which solution works best for you.

parts servos

glue bat pack and motors

install nano board

Version 0.2
Last updated 2020-12-15 02:14:03 +0100

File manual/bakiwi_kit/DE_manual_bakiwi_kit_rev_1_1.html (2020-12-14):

# Bakiwi Kit Bauanleitung

Doc Writer
kubisch@informatik.hu-berlin.de
version 0.21, 2020-12-15

bakiwi logo 3 1 dynamic DE

Abenteuer-Verzeichnis

- Vorbereitung
  - Werkzeuge
  - Bauteile sichten
  - Nimm dir Zeit!
- 1. Die Bauteile einlöten
  - 1.1. Widerstände
  - 1.2. Kondensator
  - 1.3. Schaltkreis-Sockel
  - 1.4. Taster
  - 1.5. Spannungswandler
  - 1.6. Batteriekabel-Buchsen
  - 1.7. An/Aus-Schalter
  - 1.8. Stiftleisten
  - 1.9. Leuchtdioden
  - 1.10. Elektrolytkondensator
  - 1.11. Potentiometer
  - Pause
  - 1.12. Batteriefächer
  - 1.13. Mikrocontroller
  - 1.14. Fühler
- 2. Nach dem Löten
  - 2.1. Aufräumen
  - 2.2. Abfallentsorgung
  - 2.3. Funktionstest
  - 2.4. Was tun, wenn etwas kaputt gegangen ist?
- 3. Mechanischer Zusammenbau
  - 3.1. Vorbereitung
  - 3.2. Motoren einbauen
  - 3.3. Rahmen zusammensetzen
  - 3.4. Motorkabel verbinden
  - 3.5. Batteriehalter anbringen
  - 3.6. Beine anbringen
- 4. Wie Du Dein Bakiwi spielst und wie es funktioniert
  - 4.1. Vor dem Einschalten
  - 4.2. Die Funktionsweise erklärt
  - 4.3. Laufparameter
  - 4.4. Zentrierung
  - 4.5. Der Schaltplan
- Hast du noch Fragen?

## Vorbereitung

### Werkzeuge

Für das Löten der Bakiwi-Elektronik benötigst du folgende Werkzeuge:

- Lötkolben (oder Lötstation) mit dünner Lötspitze
- Lötzinn (empfohlen: Dicke 0.5—0.75mm mit integriertem Flussmittel, bleifrei)
- Messingwolle mit Behälter ("Trockenreiniger"), alternativ ein angefeuchtetes Schwämmchen
- Seitenschneider oder Knipszange
- Multimeter (optional)

01 required tools 02 fine tip and solder

Note | Falls du noch gar keine Erfahrung im Löten hast, dann empfehlen wir dir, vorher ein Einführungsvideo oder Tutorial anzuschauen um schon mal eine ungefähre Vorstellung vom Löten zu entwickeln. Noch besser ist es, wenn du den Bausatz mit jemand anderem zusammen aufbaust, der bereits ein wenig löten kann.

### Bauteile sichten

Überprüfe alle Bauteile auf Vollständigkeit. Zusätzlich zu den gezeigten Teilen hast du vielleicht Material beiliegen, welches sich für die Fühler deines Bakiwi eignet, z.B. Gitarrensaiten oder Pfeifenputzer.

03 check electronic parts annotated DE

Lege alle Kleinteile in ein Gefäß, damit dir keines verloren gehen kann. Nimm dir zuerst die Bakiwi-Platine und leg sie vor dir hin. Die Oberseite der Platine ist die mit den Bauteilbeschriftungen. Alle Bauteile werden nun nach und nach in einzeln erklärten Schritten auf der Oberseite eingesteckt und auf der Unterseite festgelötet. Die beste Übereinstimmung mit den Bildern dieser Anleitung hast du, wenn du die Platine so drehst, dass du den Bakiwi-Schriftzug lesen kannst und sie mit der Beschriftung POWER zu dir gedreht ist und PAUSE nach oben zeigt.

04 put parts in container 05 get pcb

Schalte die Lötstation ein und überprüfe die Temperaturanzeige. Wenn die Temperatur einstellbar ist, stelle sie passend zum Legierungs-Mischungsverhältnis deines Lötzinns ein (Aufschrift beachten). Wenn du dir unsicher bist, beginne mit 330°C, abhängig von der Leistung der Lötstation ist vielleicht eine etwas höhere Temperatur nötig. Wenn sich das Löten klebrig anfühlt, dann kann die Temperatur zu niedrig sein. Erhöhe bei Bedarf die Temperatur allmählich, bis das Lot mühelos schmilzt.

Tip | Wenn deine Lötspitze auch bei stetigem Säubern nicht mehr glänzt und immer wieder dunkel wird ist die Temperatur vermutlich zu hoch eingestellt.

### Nimm dir Zeit!

Das Zusammenlöten deines Bakiwis erfordert Ruhe und Konzentration. Die benötigte Zeit ist von Mensch zu Mensch unterschiedlich und sehr vom Vorwissen abhängig. Absolute Neulinge sollte 2 Stunden für das Löten einplanen, Profis schaffen das mitunter in 30 Minuten.

## 1. Die Bauteile einlöten

### 1.1. Widerstände

Nimm dir die Widerstände zur Hand. Es gibt einen blauen Widerstand und zwei in beige. Beginne damit, das Papier an jeweils beiden Enden des blauen Widerstands abzuziehen.

01 resistors prepare resistor

Nun biege die beiden Draht-Enden mit deinen Fingern direkt an ihrem Ursprung um, sodass sie beide in dieselbe Richtung zeigen und sich die beiden Drähte parallel gegenüberstehen. Der blaue Widerstand hat die Bezeichnung R3. Suche nach dem abgebildeten Widerstandssymbol auf der Platine, es befindet sich unmittelbar unter dem Bakiwi-Schriftzug. Setze ihn wie auf dem Bild gezeigt auf der Platine ein. Ein Widerstand besitzt keine Polarität, es spielt also keine Rolle, wie herum du diesen einsetzt.

08 resistors bend 02 resistors position

Halte das eingesetzte Bauteil mit den Fingern fest, drehe die Platine vorsichtig um und leg Sie vor dir ab. Beginne nun damit, die Drahtenden auf der Platinenunterseite festzulöten. Achte dabei darauf, den Draht und die Lötfläche um das Loch gleichzeitig zu berühren und aufzuheizen während du das Lötzinn hinzufügst. Die Wärmeübertragung funktioniert am besten, wenn die Lötspitze kurz vorher gereinigt und schon etwas mit Zinn benetzt ist.

03 resistors inserted 04 resistors soldering

Entferne den überstehenden Draht, indem du ihn mit einer geeigneten Zange (z. B. Seitenschneider) abknipst. Entferne dabei den Draht möglichst knapp über deiner Lötstelle, ohne diese zu beschädigen.

05 resistors cutting 09 resistors cutting

Nun folgen die beiden anderen Widerstände R1 und R2 (beige). Sie werden links und rechts vom Schriftzug angebracht. Die Reihenfolge ist dabei egal, du kannst auch gleich beide zusammen einbauen. Die Arbeitsschritte sind die gleichen wie beim ersten Widerstand.

06 resistors repeat 07 resistors done

Gratulation. Du hast den ersten Schritt gemeistert. Vergleiche dein Ergebnis mit dem Bild aus dieser Anleitung.

### 1.2. Kondensator

Als Nächstes ist der Kondensator an der Reihe. Suche nach dem kleinen orange-farbenen Bauteil in Form einer Linse. Die Position auf der Platine ist diesmal weiter zum anderen Ende bei der Markierung C1. Schaue auf das abgebildete Symbol.

01 capacitor prepare capacitor

So wie eben bei den Widerständen wird der Kondensator von oben in die Platine gesteckt und von der Rückseite festgelötet.

02 capacitor detail 03 capacitor position

Nach dem Löten kannst du hier ebenfalls die überstehenden Draht-Enden abzwicken.

04 capacitor soldering 05 capacitor cutting

Geschafft. Dies war das Ende deiner Aufwärmrunde. Denn jetzt wird es eine Idee kniffeliger.

### 1.3. Schaltkreis-Sockel

Der Schaltkreis-Sockel hat ganze 14 Kontakte und das heißt für Dich, dass du Deine Lötfertigkeiten jetzt richtig trainieren kannst. Denn alle 14 Lötstellen sind identisch.

01 socket prepare socket

Die Position des Sockels auf der Platine kannst du nicht übersehen. Der Sockel hat auf einer Schmalseite eine kleine Kerbe und diese sollte, wie auf der Platine gekennzeichnet, nach vorne zeigen.

02 socket detail 03 socket position

Achte beim Löten darauf, dass du zunächst erst eine Ecke und dann die schräg gegenüberliegende Ecke anlötest, falls du den Sockel noch ein wenig tarieren möchtest.

04 socket soldering start 05 socket soldering done

Tada. Du hast nun bereits 22 Lötstellen auf der Bakiwi-Platine gesetzt. Wenn du bisher nicht so viel gelötet hattest, solltest du spätestens jetzt den Dreh gut raushaben.

### 1.4. Taster

Der Taster wird an der Stelle mit der Markierung PAUSE eingesetzt. Wenn du den Taster spielend leicht einsetzen kannst ohne die Beinchen zu biegen ist er auch automatisch richtig herum. Mitunter hörst du ein leises Knackgeräusch, wenn der Taster einrastet.

01 button prepare button

Important | Die Lötstifte des Tasters sind ein wenig spitz, achte beim Einsetzen des Tasters auf deine Finger. Nach dem Einlöten solltest du diese Spitzen mit der Zange entfernen.

02 button position

### 1.5. Spannungswandler

Das nächste Bauteil wird etwas schwieriger. Halte zunächst nach dem abgebildeten Symbol VREG auf der Platine Ausschau, es ist knapp über dem orangenen Kondensator zu finden und sieht aus wie ein angeschnittener Kreis.

01 vreg prepare vreg

Achtung! Jetzt wird es etwas fummelig. Der Spannungswandler hat drei dünne Beinchen, die superdicht aneinander liegen. Damit du den Spannungswandler einsetzen kannst, muss das mittlere Bein etwas in Richtung der Rundung umgebogen werden, sodass die Enden der Drähte ein kleines Dreieck aufspannen. Du kannst eine Pinzette oder einen Bleistift zur Hilfe nehmen oder es vorsichtig mit deinem Fingernagel probieren.

02 vreg bending

Die richtige Anordnung der Beinchen ist bei diesem Bauteil entscheidend für seine korrekte Funktion. Achte daher darauf, dass die Form des Bauteils mit der auf der Platine abgebildeten Zeichnung übereinstimmt. Setze den Spannungswandler ein und drücke ihn wie abgebildet Stück für Stück weiter hinein. Dabei wird sich das mittlere Beinchen noch weiter verbiegen — das ist in Ordnung.

04 vreg insert 1 05 vreg insert 2

Wenn der Spannungswandler bis auf die Platine gedrückt ist, sollte er kaum 1 mm höher sein als der Schaltkreissockel. Nun löte die drei Beine wie gehabt fest und kürze die Drähte nach dem Löten mit der Zange. Du wirst feststellen, dass die Lötstellen diesmal sehr dicht beieinander sind. Konzentriere dich gut, damit kein Kurzschluss entsteht.

06 vreg insert 3 03 vreg position

Gut gemacht. Jetzt wird das Löten erst einmal wieder etwas einfacher, versprochen.

### 1.6. Batteriekabel-Buchsen

01 batcon prepare batcon

Setze nun die zwei weißen Batteriebuchsen bei den Markierungen BAT1 und BAT2 ein. Achte dabei darauf, dass du sie genau wie auf der Platine abgebildet einsetzt. Die kleinen Lücken und Kerben an den Buchsen sind auch auf der Platine abgebildet. Die korrekte Ausrichtung ist hier sehr wichtig!

02 batcon position 03 batcon soldering

Mit ein wenig Geschick kannst du beide Buchsen im gleichen Arbeitsgang einsetzen und festlöten. Auch hier bietet es sich an, zunächst ein Beinchen festzulöten und noch mal die Ausrichtung zu korrigieren falls nötig.

Caution | Achtung! Vergleiche an dieser Stelle bitte noch einmal genau deine Platine mit den abgebildeten Fotos. Eine verkehrt herum eingelötete Batteriebuchse führt bei Anschluss der Batterie später zu einem Verpolen und endet möglicherweise in der Zerstörung von Teilen deines Bakiwi. Daher schau lieber zweimal hin.

### 1.7. An/Aus-Schalter

Weiter geht es mit dem Einsetzen des An/Aus-Schalters. Dieser ist blau/weiß und wird auf der Platine bei der Markierung POWER platziert. Wichtig ist hierbei, dass das weiße Teil Richtung off zeigt. Prinzipiell kannst du den Schalter auch andersherum einlöten, er funktioniert in beide Richtungen gleichermaßen. Stelle bloß sicher, dass er in der OFF-Position ist, d. h. dass dein Bakiwi ausgeschaltet ist, wenn wir später die Batterien einlegen.

01 switch prepare switch

Caution | Zuviel Hitze lässt den Schalter schmelzen und kann ihn unbrauchbar machen, daher achte beim Löten darauf, Stift und Lötfläche stets gleichzeitig aufzuheizen, damit der Lötvorgang kurz und effektiv ist.

02 switch position 03 switch soldering

Die Lötstifte sind recht lang und sollten nach dem Festlöten ein wenig gekürzt werden. Das Material der Schalterstifte ist auch dicker als das der anderen Bauteile, sodass du etwas mehr Kraft beim Abknipsen benötigst.

### 1.8. Stiftleisten

Widme dich nun den drei Stiftleisten. Die beiden einreihigen Stiftleisten (1x3) werden mit dem kurzen Ende von oben in die Platine bei MOT1 und MOT2 eingesteckt und wie gehabt auf der Rückseite festgelöten. An ihnen werden später die Motoren deines Bakiwi angeschlossen.

01 pinh prepare pinh

Am besten setzt du beide Stiftleisten zusammen ein, drehst dann die Platine und stellst sie wie in der Abbildung gezeigt auf die noch etwas wackeligen Stiftleisten. Achte darauf, dass die Stifte möglichst senkrecht zur Platine stehen. Wenn du zuerst an jeder Stiftleiste nur einen Stift festlötest, kannst du die genaue Position durch nochmaliges Aufheizen korrigieren, sollte sie nicht gleich beim ersten Mal gerade sein.

02 pinh position 03 pinh soldering

Die doppelreihige Stiftleiste (2x3) wird bei PROG ebenfalls mit Ihrem kurzen Ende von oben eingesetzt. Das Einlöten sollte nun einfacher sein, weil die beiden verlöteten einreihigen Stiftleisten bereits die Platine stabilisieren. Die doppelreihige Stiftleiste ist der Programmieranschluss, falls du später das Programm deines Bakiwi verändern möchtest.
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

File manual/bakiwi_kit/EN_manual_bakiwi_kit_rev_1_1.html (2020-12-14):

# Bakiwi Kit Assembly Manual

Doc Writer
kubisch@informatik.hu-berlin.de
version 0.21, 2020-12-15

(Translation provided by Sebastian Schmölling and Mamun Azmy)

bakiwi logo 3 1 dynamic EN

Table of Adventures

- Preparation
  - Tools
  - View components
  - Take your time!
- 1. Solder the components
  - 1.1. Resistors
  - 1.2. Capacitor
  - 1.3. Circuit Socket
  - 1.4. Button
  - 1.5. Voltage Regulator
  - 1.6. Battery cable sockets
  - 1.7. Power Switch
  - 1.8. Pin Headers
  - 1.9. Light emitting diodes
  - 1.10. Electrolytic Capacitor
  - 1.11. Potentiometer
  - Take a Break
  - 1.12. Battery Compartments
  - 1.13. Microcontroller
  - 1.14. Antennae
- 2. After Soldering
  - 2.1. Clean Up
  - 2.2. Waste Disposal
  - 2.3. Testing
  - 2.4. What to do when something is broken?
- 3. Mechanical assembly
  - 3.1. Preparation
  - 3.2. Install Motors
  - 3.3. Putting the frame together
  - 3.4. Connect the Motor Cables
  - 3.5. Attach battery holder
  - 3.6. Attach Legs
- 4. How to play your bakiwi and how it works
  - 4.1. Before Switching on
  - 4.2. The Functionality Explained
  - 4.3. Gait Parameters
  - 4.4. Centering
  - 4.5. Schematics
- Do you have any questions?

## Preparation

### Tools

You will need the following tools to solder the Bakiwi electronics:

- Soldering iron (or station) with a thin solder tip
- Tin solder (recommended: thickness 0.5-0.75mm with integrated flux, lead-free)
- Brass wool with container ("dry cleaner"), alternatively a moistened sponge
- Diagonal cutters or pliers
- Multimeter (optional)

01 required tools 02 fine tip and solder

Note | If you have no soldering experience at all, we recommend that you watch an introductory video or tutorial beforehand in order to get a rough idea of soldering. It is even better if you assemble the kit with someone else who can already do a little bit of soldering.

### View components

Check all components for completeness. In addition to the parts shown, you may have included material that is suitable for the antennae of your Bakiwi, e. g. pieces of guitar strings or pipe cleaners.

03 check electronic parts annotated EN

Put all the small parts in a container so that none can be lost. First, take the Bakiwi board and place it in front of you so you can read the Bakiwi label. The top of the board is the one with all the component labels. All components will now be inserted and soldered one by one in individually explained steps. Each component is inserted from the top and soldered on the bottom.

04 put parts in container 05 get pcb

Turn on the soldering station and check the temperature display. If the temperature is adjustable, set it to match the recommended temperature of your solder (note the label). If you are unsure, start with 330°C, depending on the performance of the soldering station, a slightly higher temperature may be necessary. If the soldering feels sticky, then the temperature might be too low. If needed, gradually increase the temperature until the solder melts easily.

Tip | If your soldering tip no longer shines even with constant cleaning and keeps getting dark, the temperature is probably set too high.

### Take your time!

Soldering your Bakiwi requires calm and concentration. The time required varies from person to person and depends very much on previous knowledge. Absolute newbies should plan 2 hours for soldering, professionals can do it in 30 minutes.
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

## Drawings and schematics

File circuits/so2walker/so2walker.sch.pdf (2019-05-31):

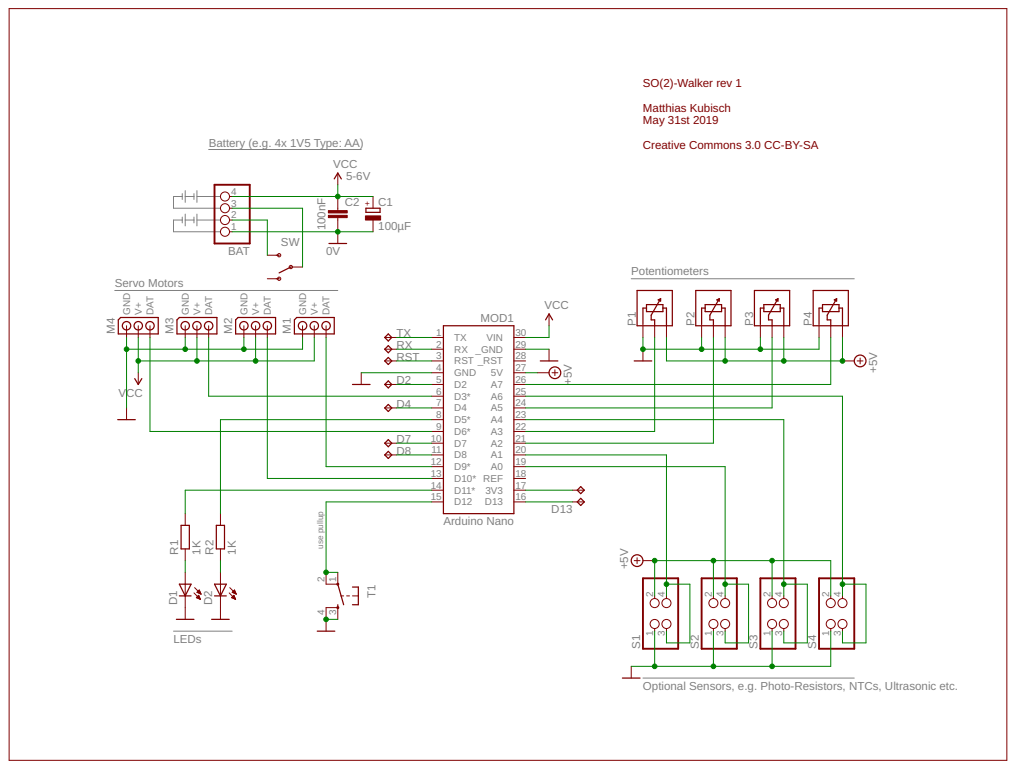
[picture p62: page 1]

SO(2)-Walker rev 1
Matthias Kubisch
May 31st 2019
Creative Commons 3.0 CC-BY-SA

Optional Sensors, e.g. Photo-Resistors, NTCs, Ultrasonic etc.

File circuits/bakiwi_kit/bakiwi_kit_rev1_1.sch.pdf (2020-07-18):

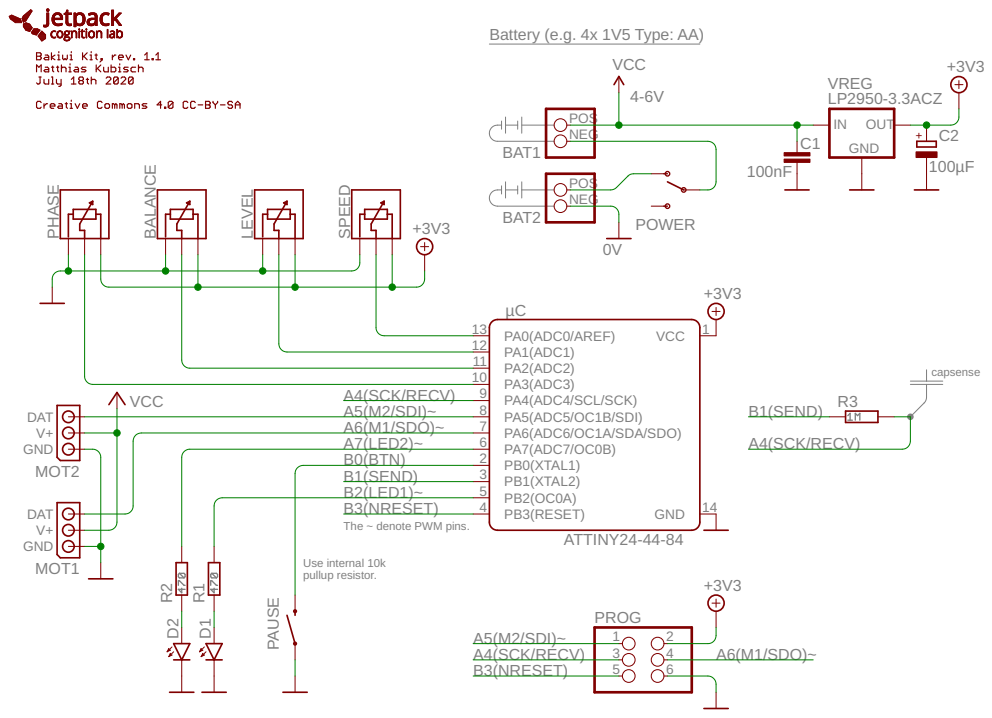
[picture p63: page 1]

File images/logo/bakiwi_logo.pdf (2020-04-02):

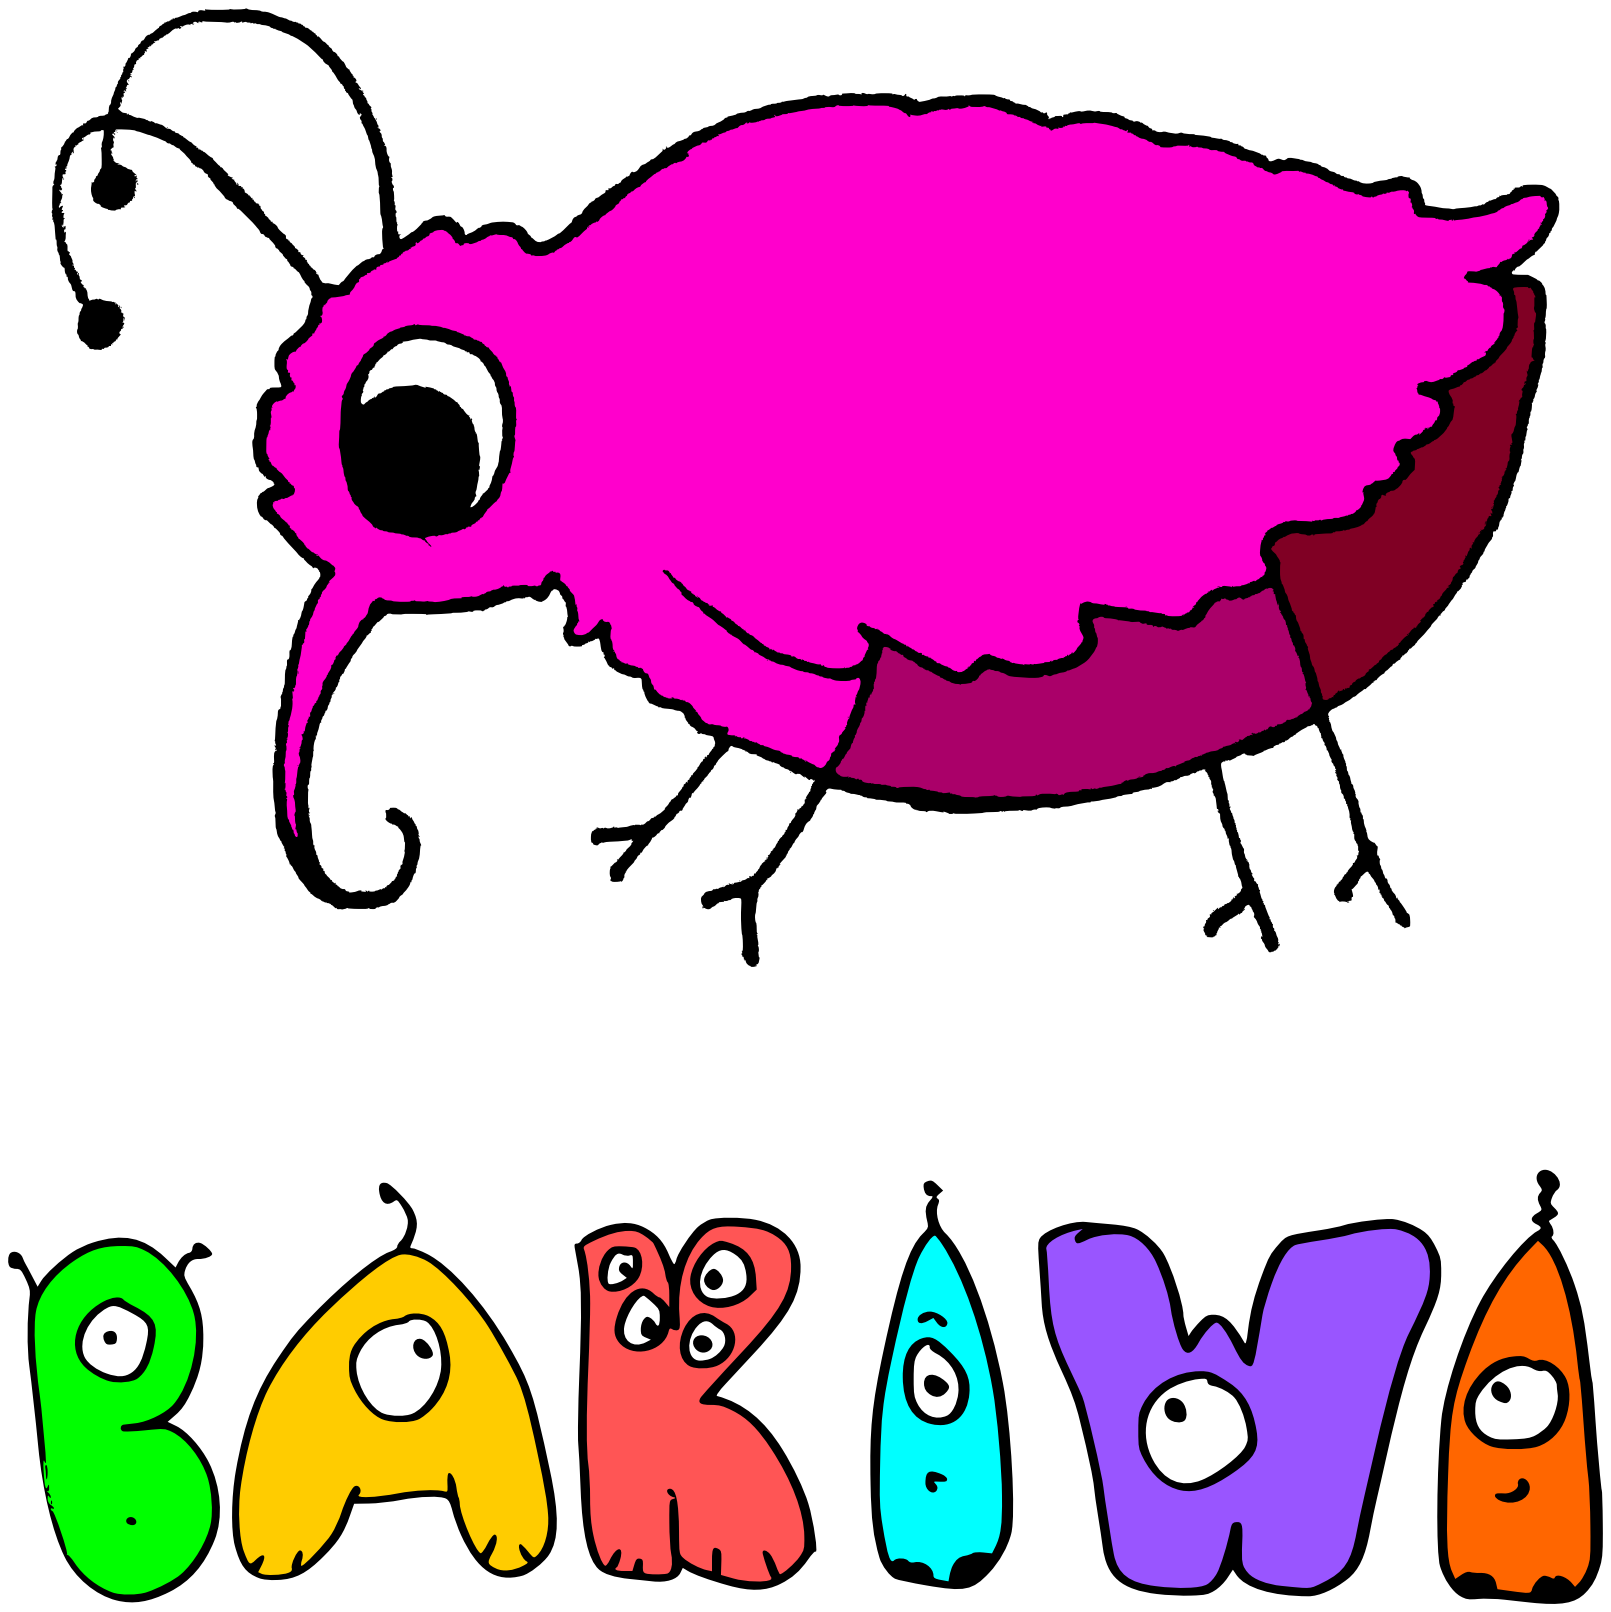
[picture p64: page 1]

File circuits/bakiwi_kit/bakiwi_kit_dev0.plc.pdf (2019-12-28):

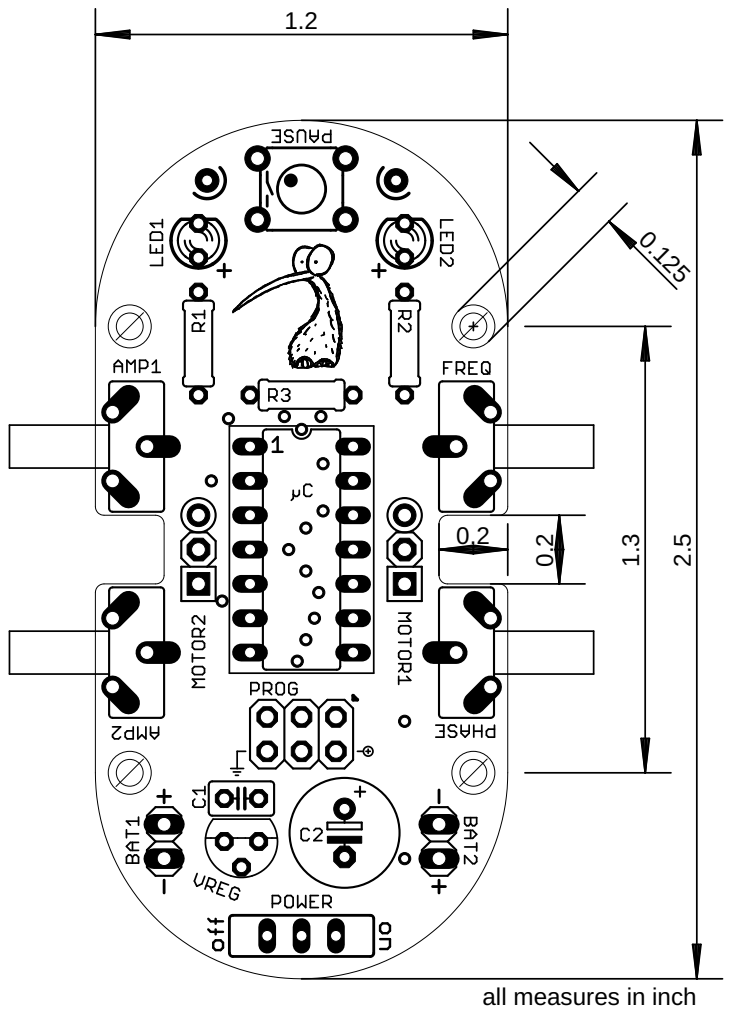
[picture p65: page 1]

all measures in inch

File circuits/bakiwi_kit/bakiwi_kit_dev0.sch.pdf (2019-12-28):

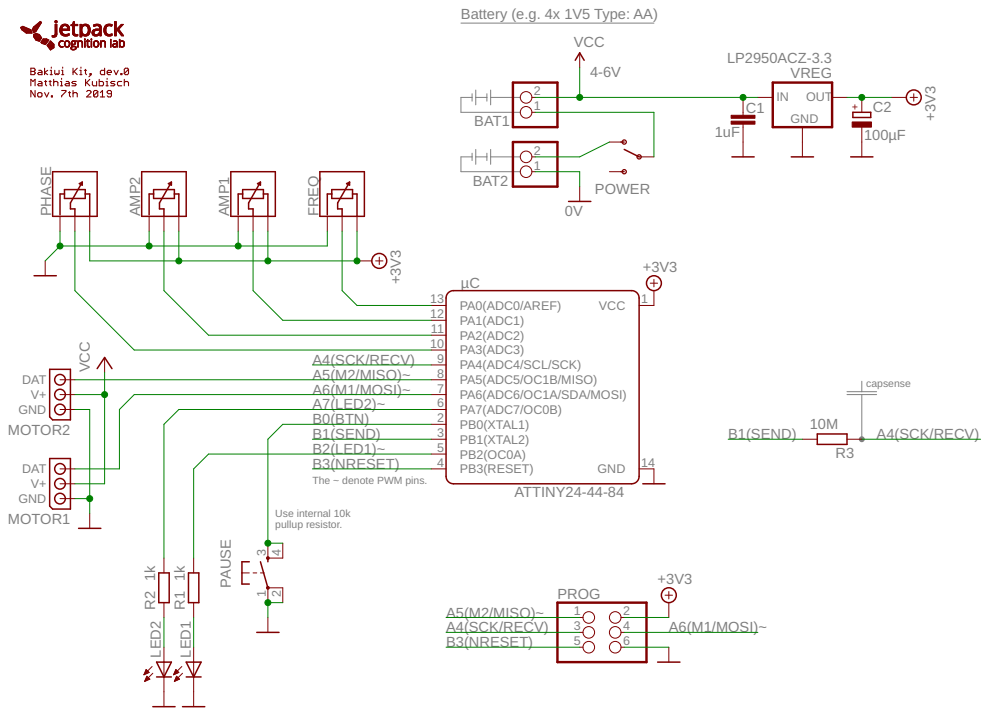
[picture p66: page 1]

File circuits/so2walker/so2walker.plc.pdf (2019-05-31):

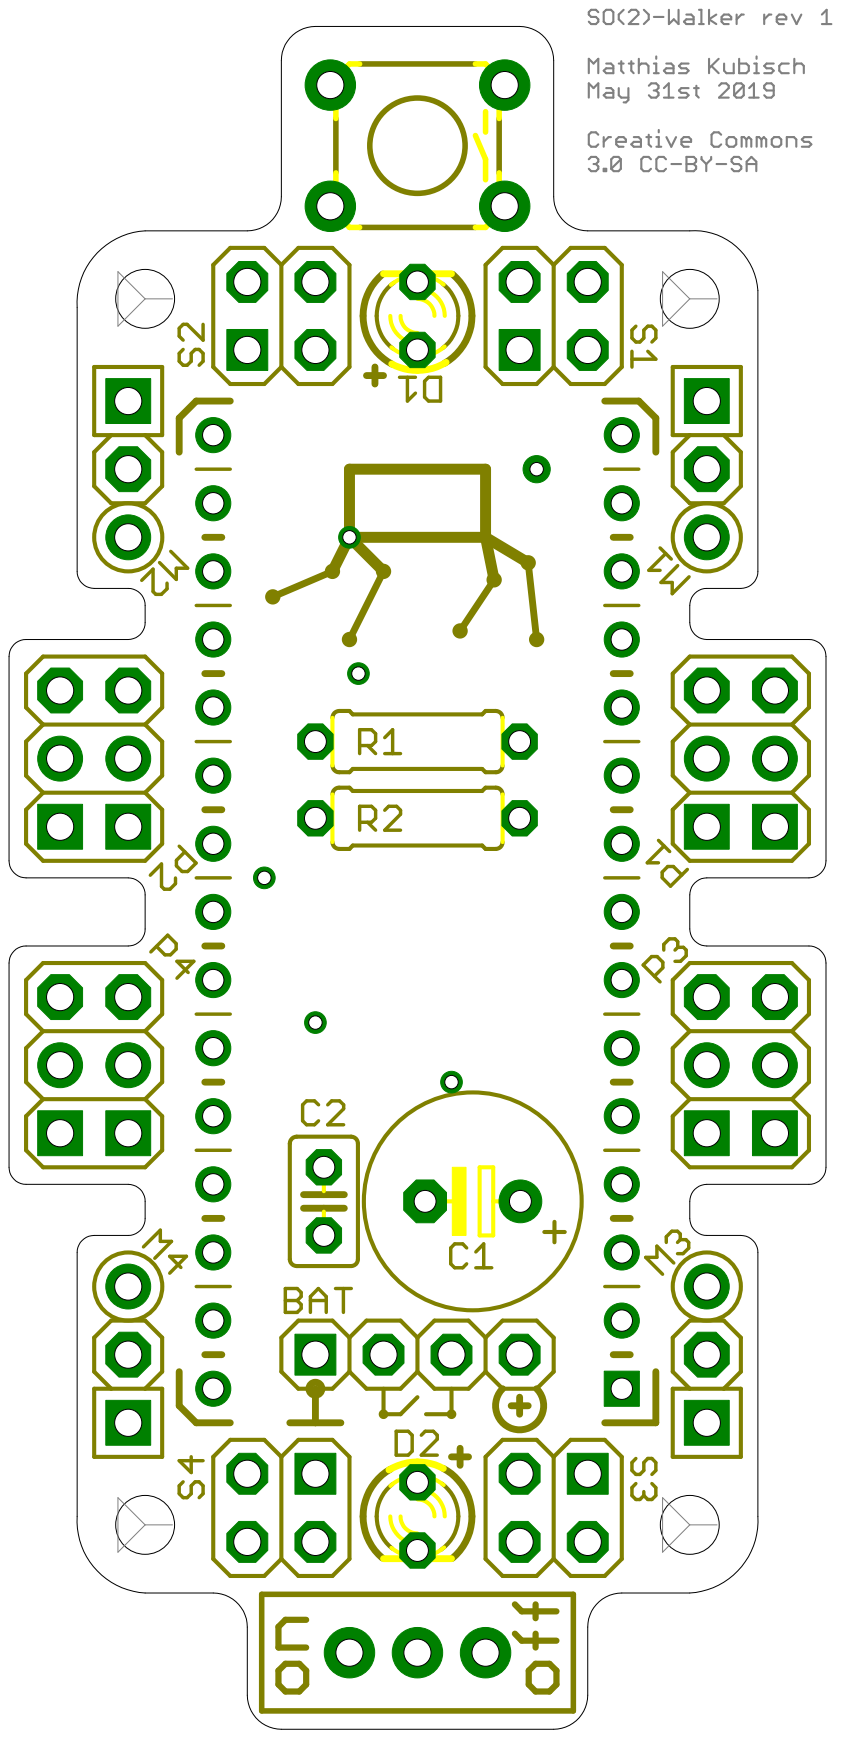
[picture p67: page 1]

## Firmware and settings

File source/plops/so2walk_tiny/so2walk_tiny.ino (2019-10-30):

/* SO(2)-Walker for Plops
 * 
 * written by Matthias Kubisch
 * Version for plops 0.01
 * Oct 30th, 2019
 * 
 *
 * TODO: 
 * + correct amplitude when playing a low freq. (amp is very low here)
 * + create board file ad cleanup code
 */


#include "jcl_tinyservo.h"
#include "jcl_switchpot.h"
#include "jcl_neural_osc.h"
//#include "jcl_plops.h"


/* LED + button */
#define LEDBTN 2

/* motors */
#define MOTOR_1 0
#define MOTOR_2 1

/* potis */
#define POTI_1 A2
#define POTI_2 A3

#define PREAMP 1.4f
#define MAX_ANGLE 90
#define WAIT_US 20000

/* timing */
unsigned long timestamp = 0;

bool pressed = false;
volatile bool paused = true;

jcl::Tinyservo motor_1;
jcl::Tinyservo motor_2;

jcl::SwitchPot poti_1(POTI_1, /*init1:*/.5f, /*init1:*/.5f); //amplitude
jcl::SwitchPot poti_2(POTI_2, /*init1:*/.5f, /*init2:*/.5f); //freq+phase

jcl::NeuralOscillator osc;

bool button_pressed() {
  static int integ = 0;
  pinMode(LEDBTN, INPUT_PULLUP);
  bool buttonstate = !digitalRead(LEDBTN);
  pinMode(LEDBTN, OUTPUT);

  integ += buttonstate ? 1 : -1;
  integ = constrain(integ, 0, 10);
  
  return integ>=5;
}

void setup() {
  /* interrupt for refreshing the servos */
  OCR0A = 0x7F;            
  TIMSK |= _BV(OCIE0A);    // enable compare interrupt (see below)
  
  pinMode(LEDBTN, OUTPUT);
  
  osc.set_frequency(poti_2.get_1st());
  osc.restart();
}

void loop() {

  /* pause, if button was pressed before and then released */
  bool state = button_pressed();
  if (pressed and !state)
  {
    if (paused) {
      paused = false;
      motor_1.attach(MOTOR_1);
      motor_2.attach(MOTOR_2);      
      poti_1.set(false);
      poti_2.set(false);
      osc.restart();
    } else {
      paused = true;
      
      motor_1.detach();
      motor_2.detach();
      poti_1.set(true);
      poti_2.set(true);
    }
  }
  pressed = state;

  poti_1.step();
  poti_2.step();

  /* propagate neural oscillator */
  osc.set_frequency(poti_2.get_1st());
  osc.step();
  

  /* read desired phase and create phase shifted motor signals */
  const float phase = 2*poti_2.get_2nd() - 1.f;

  /* create phase shifted motor signals */
  const float u1 = osc.x1;
  const float u2 = osc.get_phase_shifted_x1(phase);

  /* read desired amplitudes */
  const float lev = poti_1.get_1st();
  const float dif = poti_1.get_2nd();
  
  const float amp1 = PREAMP * lev * dif;
  const float amp2 = PREAMP * lev *(1.f - dif);

  /* calc motor outputs */
  const uint8_t out_1 = constrain(round( u1*amp1*MAX_ANGLE ) + MAX_ANGLE, 0, 2*MAX_ANGLE);
  const uint8_t out_2 = constrain(round( u2*amp2*MAX_ANGLE ) + MAX_ANGLE, 0, 2*MAX_ANGLE);

  /* write motors */
  if (!paused) {
    motor_1.write(out_1);
    motor_2.write(out_2);
  }

  /* set LED output */
  if (u1 > .0f) {
    pinMode(LEDBTN, INPUT_PULLUP);
  }
  else {
    pinMode(LEDBTN, OUTPUT); 
    digitalWrite(LEDBTN, LOW);
  }
  
  /* loop delay, wait until timer signals next 10ms slot is done */
  while(micros() - timestamp < WAIT_US);
  timestamp = micros();
  
}


/* gets called once every 2 milliseconds */ 
volatile uint8_t dt = 0;

SIGNAL(TIMER0_COMPA_vect)
{  
  ++dt;
  if (dt >= 10) { // apply the servos every 20 milliseconds
    dt = 0;
    if (!paused) {
      motor_1.apply();
      motor_2.apply();
    }
  }
}

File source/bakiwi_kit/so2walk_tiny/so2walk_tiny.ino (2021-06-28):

/*---------------------------------+
 | Bakiwi Kit Firmware             |
 | Jetpack Cognition Lab           |
 | Matthias Kubisch                |
 | kubisch@informatik.hu-berlin.de |
 | board ver. bakiwi kit rev 1.1   |
 | version 20.6.17                 |
 +---------------------------------*/

/*---WE THANK OUR SUPPORTERS-----------------------------------------------+
 | Daniel Sitbon, Thomas Lobig, Sebastian Schmölling, Martin Marmulla,     |
 | Richard Lemke, Jens Priebe, Ines Müller, Stefan Kruse, Thomas Chung,    |
 | Andreas Gerken, Oswald Berthold, Pablo Zöllner, Andreas Pieper,         |
 | Hannes Ziegerhofer, Philip Brechler, Rebecca Miko, Wally WonTaek Chung, |
 | Michael Merz, Sian Thomas, Gero, HealthCare Futurists, Bruno Böttcher,  |
 | Andrea Mayr-Stalder, Irene Diez, Guido Schillaci, MaggiWuerze,          |
 | Heinrich Mellmann, Christian Thiele, Michael Mehling, Hendrik Schober,  |
 | xHain hack+makespace, Mona Orgel, Paula Grünwald, Thomas Prätzlich,     |
 | Karen Ellmer, Jasper Mendel, Mamoun Azmy, Mali Ohana, Olivier Haustrate,|
 | Clemenz Kühn, Elisa Fett, Mario Lasseck, Basti Voss, Jaqueline Reiter,  |
 | Thomas Schranz, Oskar Obereder, Wendelin Weingartner, Sophie Fee Thomas |
 | Hime Yoshimura, Mirco Eidecker, MINT-Impuls, Verstehbahnhof, CCCamp19   |
 | Elmar Janosch Wander                                                    |
 +-------------------------------------------------------------------------*/


#include "jcl_neural_osc.h"
#include "jcl_bakiwi_kit_rev_1_1.h"


bool pressed = false;
volatile bool paused = true;

using namespace jcl;

NeuralOscillator osc;
BakiwiKit        bakiwi;

void setup() {

  bakiwi.init(); /* initialize bakiwi board */

  osc.set_frequency(bakiwi.get_frq());
  osc.restart();

  /* start LED boot-up sequence */
  for (float i = 255; i > 2; i *= 0.95) {
    bakiwi.leds_set_pwm((uint8_t)i, (uint8_t)i);
    delay(5);
  }

  bakiwi.leds_off();
}

void loop() {

  bakiwi.step();

  /* pause, if button was pressed before and then released */
  bool state = bakiwi.button_pressed();
  if (pressed and !state)
  {
    if (paused) {
      paused = false;
      bakiwi.motors_on();
      osc.restart();
    } else {
      paused = true;
      bakiwi.motors_off();
    }
  }
  pressed = state;

  /* read capacitive sensors (aka antennas) */
  const float cs = bakiwi.cap.get();

  /* reduce frequency when antennas touched */
  const float freq_gain = (cs > 0) ? (1 - 5 * clamp(cs, 0.f, .2f))
                                   : (1 - 0.334 * cs);

  /* reduce amplitude when antennas touched */
  const float ampl_gain = 1 - clamp(cs, 0.f, 1.f);

  /* propagate neural oscillator */
  osc.set_frequency(freq_gain * bakiwi.get_frq());
  osc.step();

  /* read phase */
  const float phase = 2 * bakiwi.get_phs() - 1;

  /* create phase shifted motor signals */
  const float u1 = osc.x1;
  const float u2 = osc.get_phase_shifted_x1(phase);

  /* read amplitude and balance */
  const float lev = bakiwi.get_amp() * ampl_gain;
  const float dif = 2 * bakiwi.get_bal();

  /* set amplitudes for front (1) and rear (2) motor */
  const float amp1 = lev * clamp(    dif, .0f, 1.f);
  const float amp2 = lev * clamp(2 - dif, .0f, 1.f);

  /* prepare motor outputs */
  const uint8_t out_1 = clamp((unsigned) (round(u1 * amp1 * DEG90) + DEG90 + bakiwi.bias_1), 0u, 2 * DEG90);
  const uint8_t out_2 = clamp((unsigned) (round(u2 * amp2 * DEG90) + DEG90 + bakiwi.bias_2), 0u, 2 * DEG90);

  /* write motors */
  if (not paused)
    bakiwi.write_motors(out_1, out_2);

  /* prepare LED pwms */
  uint8_t led_1, led_2;
  if (cs < 0.25) { // if antennas not touched
    led_1 = 255 * clamp(u1 * amp1 * 4, 0.f, 1.f); // blink LEDs with oscillator state
    led_2 = 255 * clamp(u2 * amp2 * 4, 0.f, 1.f);
  } else {
    led_1 = 255 * clamp(cs, 0.f, 1.f); // light-up LEDs according to antenna touch
    led_2 = 255 * clamp(cs, 0.f, 1.f);
  }

  bakiwi.leds_set_pwm(led_1, led_2);

  bakiwi.wait_for_next_cycle();
}

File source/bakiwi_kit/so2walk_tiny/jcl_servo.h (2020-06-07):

#ifndef JCL_SERVO_H
#define JCL_SERVO_H

/*---------------------------------+
 | Minimal Servo Lib               |
 | Jetpack Cognition Lab           |
 | Matthias Kubisch                |
 | kubisch@informatik.hu-berlin.de |
 | June 5th 2020                   |
 +---------------------------------*/


#include <avr/interrupt.h>
#include "Arduino.h"
#include "jcl_modules.h"

/* This is a minimal two-servo class for attiny84/atmega328p (Bakiwi Kit)
 * It is NOT meant as a full library. Parts of the code is inspired by servo
 * libs with contributions of Jim Studt, David A. Mellis, and Paul Stoffregen. */

#if defined(__AVR_ATtiny84__)
 #define SERVO_PIN_A 6
 #define SERVO_PIN_B 5
#elif defined(__AVR_ATmega328P__)
  #define SERVO_PIN_A 9
  #define SERVO_PIN_B 10
#else
  static_assert(false, "no servo pins assinged");
#endif


namespace jcl {

/*-------------------------------------------+
 |  default pulse lengths [in us] for degree |
 |   0: 544                                  |
 | 180: 2400                                 |
 +-------------------------------------------*/

const uint16_t pulse_min = 544;
const uint16_t pulse_max = 2400;
const uint16_t a = clockCyclesPerMicrosecond() * pulse_min;
const uint16_t b = clockCyclesPerMicrosecond() * (pulse_max - pulse_min) / 180;


class JCLServoBase {
  static bool is_attached_A, is_attached_B;
};


bool JCLServoBase::is_attached_A = false;
bool JCLServoBase::is_attached_B = false;


template <uint8_t PIN>
class JCLServo : public JCLServoBase
{

  static void init_timer(void)
  {
    const uint8_t defSREG = SREG;

    cli();
    TCCR1A = _BV(WGM11);
    TCCR1B = _BV(WGM12)
           | _BV(WGM13)  /* Mode: Fast PWM, ICR1 is top */
           | _BV(CS11);  /* Clock Prescaler is /8       */

    OCR1A = 3000;
    OCR1B = 3000;
    ICR1  = clockCyclesPerMicrosecond()*(20000L/8);  /* ICR1 is 16bit, so its value is
                                                        e.g. 16*20000/8 = 40000, for 16MHz clock
                                                        20000us is servo refresh time
                                                        /8 is the prescaler. */

    TIMSK1 &=  ~(_BV(OCIE1A) | _BV(OCIE1B) | _BV(TOIE1) );

    SREG = defSREG;  // restore
  }


 public:

  JCLServo() {
    static_assert(PIN == SERVO_PIN_A or PIN == SERVO_PIN_B);
  }

  /* attaches servo to a pin, sets pin mode and timer output but
   * will not position the servo until a subsequent write() */
  void on(void)
  {
    digitalWrite(PIN, LOW);
    pinMode(PIN, OUTPUT);

    if (!is_attached_A && !is_attached_B) init_timer();

    if (PIN == SERVO_PIN_A) {
      is_attached_A = true;
      TCCR1A = (TCCR1A & ~_BV(COM1A0)) | _BV(COM1A1);
    }

    if (PIN == SERVO_PIN_B) {
      is_attached_B = true;
      TCCR1A = (TCCR1A & ~_BV(COM1B0)) | _BV(COM1B1);
    }
  }


  void off()
  {
    if (PIN == SERVO_PIN_A) {
      is_attached_A = false;
      TCCR1A = TCCR1A & ~_BV(COM1A0) & ~_BV(COM1A1);
      pinMode(PIN, INPUT);
    }

    if (PIN == SERVO_PIN_B) {
      is_attached_B = false;
      TCCR1A = TCCR1A & ~_BV(COM1B0) & ~_BV(COM1B1);
      pinMode(PIN, INPUT);
    }
  }

  /* sets the servos target angle from 0 to 180 deg */
  void set(uint8_t angle)
  {
    clamp(angle, uint8_t{0}, uint8_t{180});

    /* 8L is TCNT1 prescaler, change if the clock's prescaler changes */
    const uint16_t p = (a + b * angle) / 8;

    if (PIN == SERVO_PIN_A) OCR1A = p;
    if (PIN == SERVO_PIN_B) OCR1B = p;
  }


};

} /* namespace jcl */

#endif /* JCL_SERVO_H */

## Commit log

2019-05-20 added arduino source.
2019-05-31 added circuit and math.
2019-05-31 updated board layour png.
2019-06-03 title image, brief explanation and bom.
    [so2walker.bom.ods]
2019-09-16 increased adjustable phase angle from -90,+90 to -180,+180; used timer instead of delay for loop timing.
2019-09-26 adding chirp explanation, using timer 2 in so2walk and softly pulsing the second led.
2019-10-14 Bakiwi 2 framework initial draft.
2019-10-17 doc: how to set board and uC.
2019-12-19 improved capacitive sensor reading.
2019-12-28 added circuit description.
2020-02-22 fixed totoro melody, buzzer play, balance poti, 10ms timeloop, non-blocking tof sensor readout.
    [bakiwi_rev2.0.h, so2walk_rev2.0.ino]
2020-04-02 moving files.
    [so2walker.bom.ods]
2020-04-02 added some hardware parts for kit dev0
    [BatterySaddleBakiwi2_SUPPORT.stl, Case1.stl, Case2.stl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]
2020-04-03 repo cleanup, adding sep. logo file
    [bakiwi_kit_rev1_1.bom.ods]
2020-04-03 updated bom, added eagle brd file for pcb manufacturing.
    [so2walker.bom.ods, so2walker.brd]
2020-05-04 replaced horn, added champher
    [servo_to_lego_5x5.stl]
2020-05-04 updated schematics.
2020-05-04 adding draft of soldering part for the assembly manual.
2020-05-05 Update manual_bakiwi_kit_rev_1_1.adoc
    Ich war grade in Korrekturlaune und habs mal ein wenig gebürstet, feel free to reject if not convinced
2020-05-05 added examples for antennas
2020-05-25 added draft for second part of the manual.
    [bakiwi_kit_rev1_1.bom.ods]
2020-05-28 created configuration routine for calibrating angle offet.
2020-06-01 refactored servo lib, saving weight gain + system starts.
2020-06-07 removed pwmservo lib.
2020-06-07 updating hardware parts.
    [clamp_nut.stl, frame_base.stl, frame_lid.stl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]
2020-06-07 deleting old hardware files.
    [BatterySaddleBakiwi2_SUPPORT.stl, Case1.stl, Case2.stl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]
2020-06-11 beta release for assembly manual (german)
2020-06-17 renamed hw to parts
    [clamp_nut.stl, frame_base.stl, frame_lid.stl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]
2020-07-18 replaced old SPI signal names.
2020-10-09 assembly manual EN (beta)
2020-10-09 added annotated picture for assembly overview in english.
2020-12-14 landing page in html.
2020-12-15 updated landing page
2020-12-15 adding cut stencil
    [cut_stencil.stl]
2020-12-15 correct folders for stencils
    [cut_stencil.stl]
2021-02-04 added picture with flasher device.

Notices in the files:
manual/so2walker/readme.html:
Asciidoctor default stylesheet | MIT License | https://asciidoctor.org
